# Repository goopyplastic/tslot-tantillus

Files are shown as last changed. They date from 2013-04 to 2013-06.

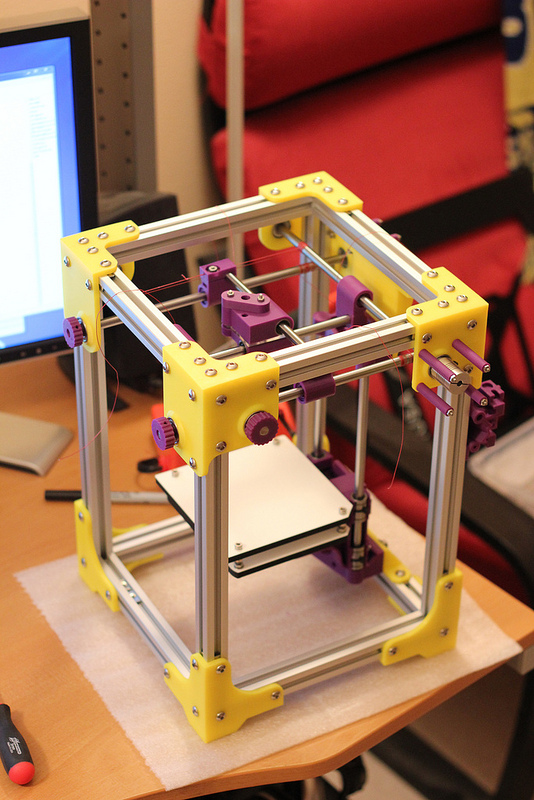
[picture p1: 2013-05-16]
photo.jpg

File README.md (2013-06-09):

tslot-tantillus
===============

T-Slot frame for Tantillus 3D Printer

Initial Version Assumes:

- That you are using the cable version of the Z axis. If you aren't you will need to modify the lower Z adaptor for motor mount holes.
- 40mm standoffs for motor mounts, can purchase at mcmaster or print your own. Use 3x50mm bolts to attach motors.
- Misumi 2020 T-Slot lengths:
     - 8x HFS5-2020-200 (Horizontal 200mm)
     - 4x HFS5-2020-335 (Vertical 335mm)
     - HNKK5-5 (T-Slot nuts)
     - M5 10mm button head screw to affix panels to frame
- 8mm Shafting
     - 2x SFJ8-170 (8x170mm bearing shafts, same as Tantillus internal XY axis)
     - 2x SFJ8-230 (8x230mm bearing shafts, same as Tantillus Z axis)
- 5/16" Shafting
     - 2x 277mm
     - 2x 277mm with holes drilled 56.5mm in from each end for a distance of 164mm hole to hole
- Couplers
     - 2x Aluminum or simlar 5mm to 8mm shaft couplers
- Frame extra STL's:
     - spacers.STL - Motor 40mm standoffs if you want to use printed ones
     - knob_fixed.stl - Collar/manual nob for end of 5/16" rod (Use m3 set screw to hold in place on shaft.)
     - fanmount_fixed.stl x2 - Clips to attach fans to t-slot
     - lcdclamp_fixed.stl x2 - Clips to use as a rest for http://www.thingiverse.com/thing:28767
     - megaholder_fixed.stl - Plate for attaching arduino mega to t-slot
- The following files are provided for convenience:
     - ZlowerbracketfixedMETRIC_fixed.stl - Cable Z bracket modd'ed for M5 mounting (Use M5 16mm and M5 nuts)
     - ZupperbracketfixedMETRIC_fixed.stl - Cable Z bracket modd'ed for M5 mounting (Use M5 16mm and M5 nuts)

BEEFY Z Option:

- Is a more rigid Z axis mounting that has some other advantages such as being able to slide the upper and lower mount around and clamping bar end holders.
- BEEFY Z Printed parts
     - Zlowerbracket_BEEFY.stl - Cable Z bracket modd'ed for M5 mounting (Mounts directly into 2060 T-Slot)
     - Zupperbracket_BEEFY.stl - Cable Z bracket modd'ed for M5 mounting (Mounts directly into 2060 T-Slot)
- Misumi 2060 T-Slot Lengths:
     - 1x HFS5-2060-295 (Vertical 295mm [40mm short of main uprights)
- Misumi 90 degree brackets:
     - 4x HBLFSN5
I'm often in #reprap as goopyplastic if you have questions!

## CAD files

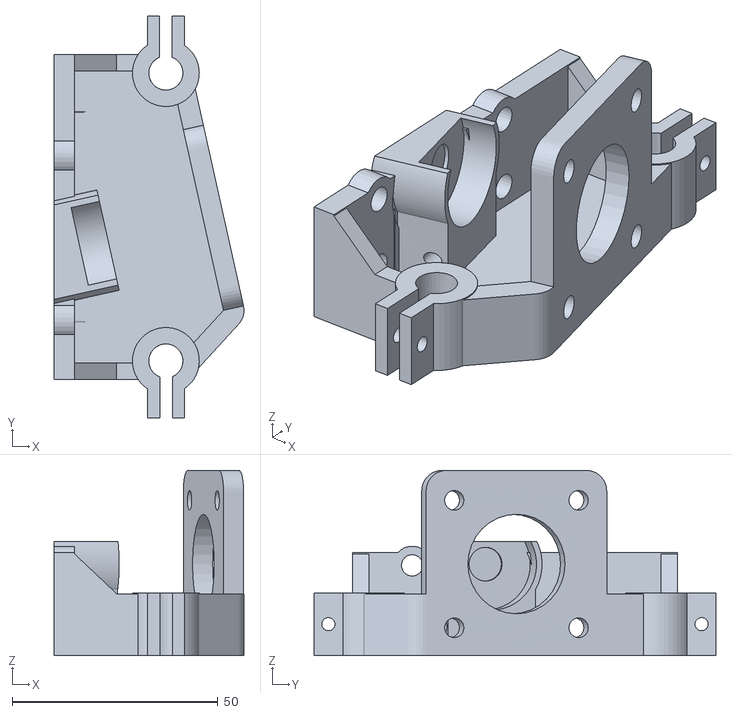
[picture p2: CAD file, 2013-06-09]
Zlowerbracket_BEEFY.stl
46.2 x 97.7 x 45.0

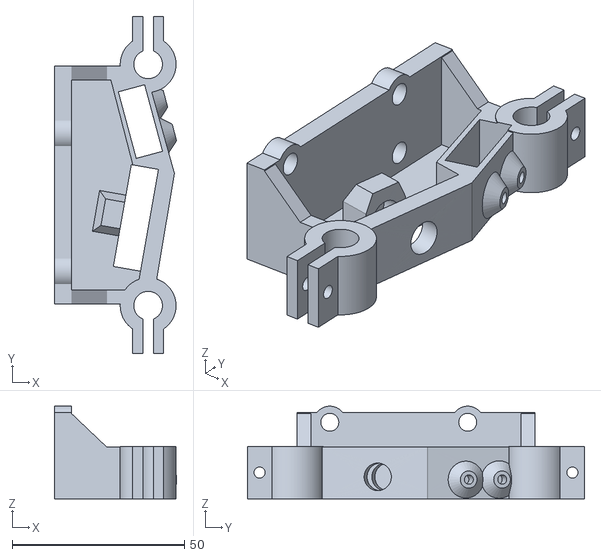
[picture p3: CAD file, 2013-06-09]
Zupperbracket_BEEFY.stl
35.5 x 97.8 x 26.9

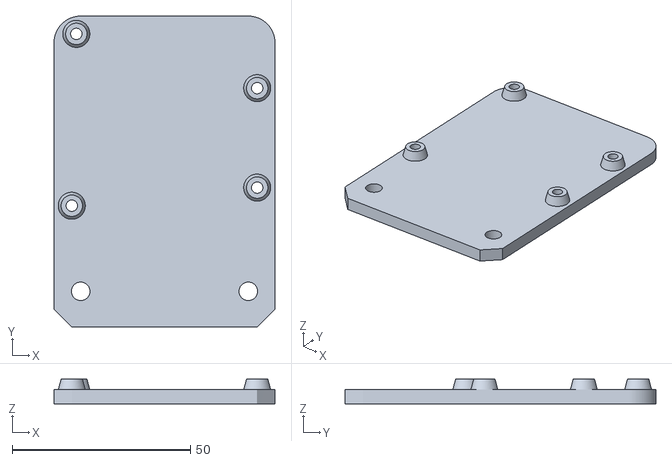
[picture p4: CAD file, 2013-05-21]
megaholder_fixed.stl
62.1 x 87.3 x 7.00

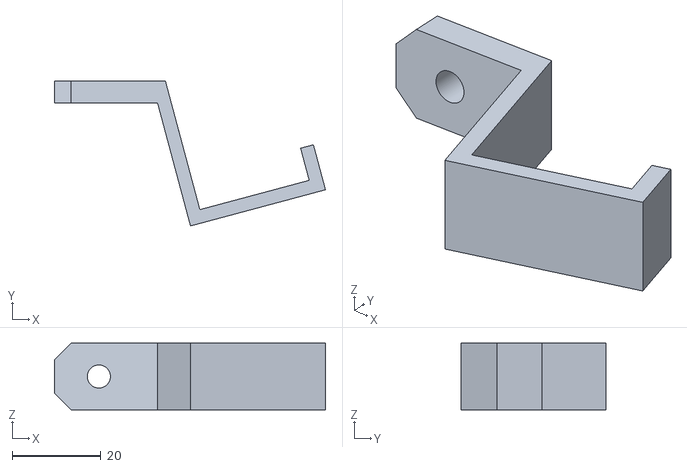
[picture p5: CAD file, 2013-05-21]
lcdclamp_fixed.stl
61.1 x 32.7 x 15.0

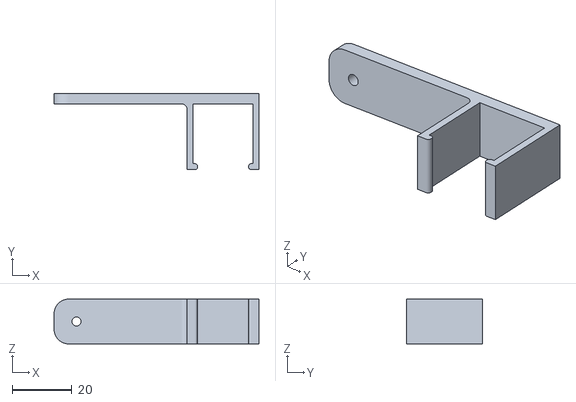
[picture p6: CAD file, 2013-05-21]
fanmount_fixed.stl
68.5 x 25.5 x 15.0

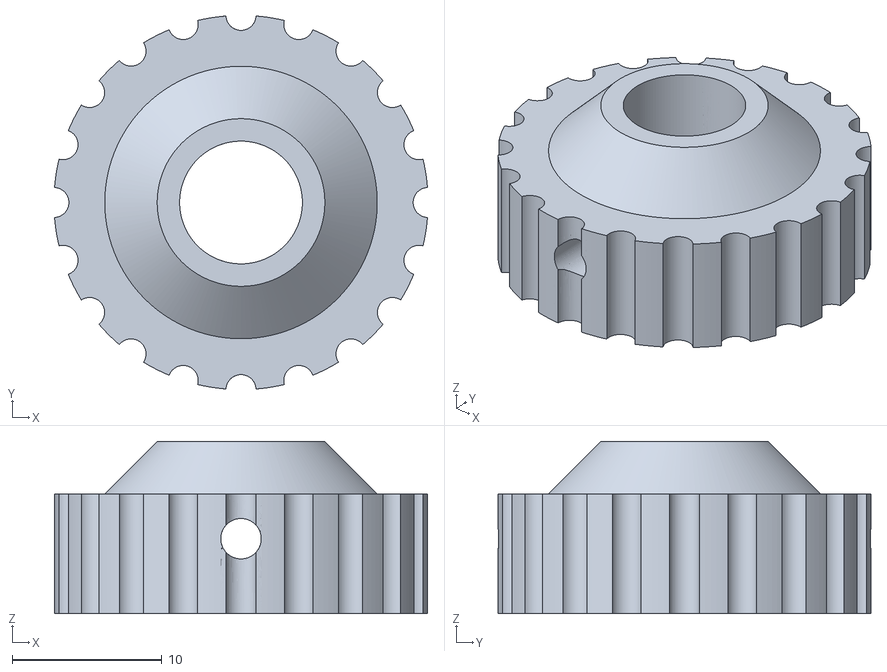
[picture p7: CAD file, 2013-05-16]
knob_fixed.stl
24.9 x 24.9 x 11.5

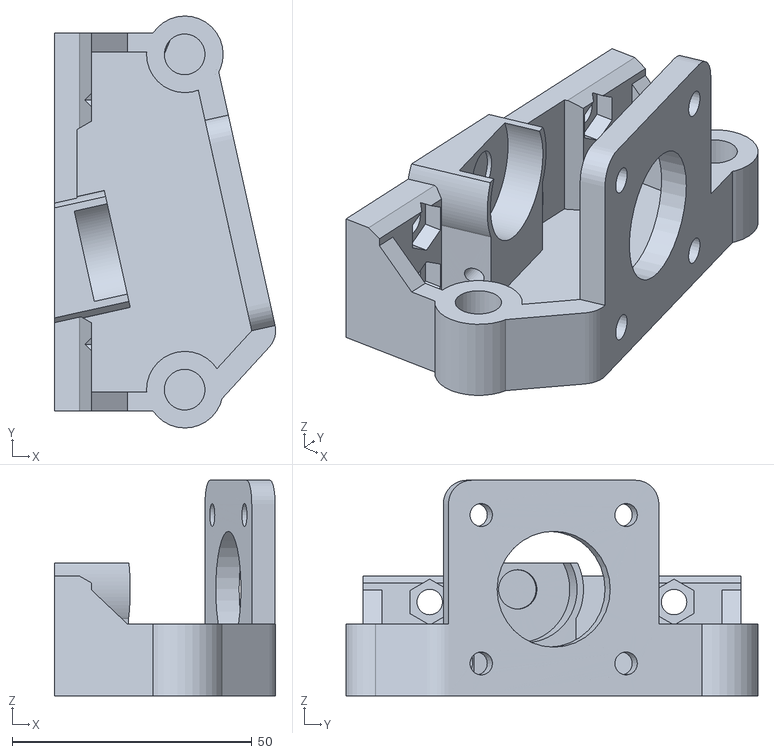
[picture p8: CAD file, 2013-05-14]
ZlowerbracketfixedMETRIC_fixed.stl
46.2 x 86.0 x 45.0

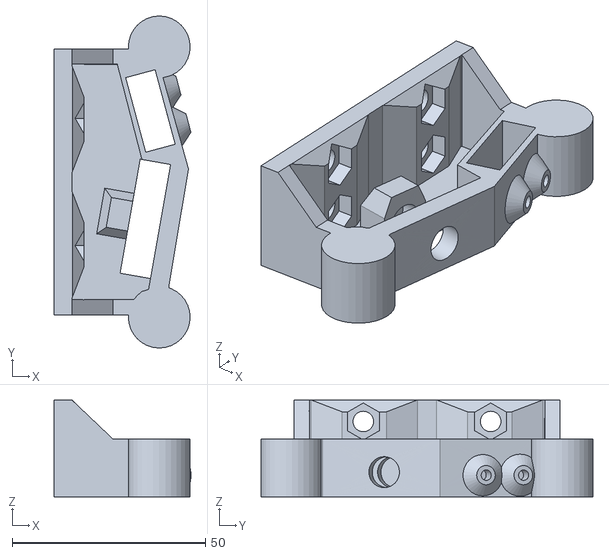
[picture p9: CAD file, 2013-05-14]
ZupperbracketfixedMETRIC_fixed.stl
35.5 x 86.0 x 25.0

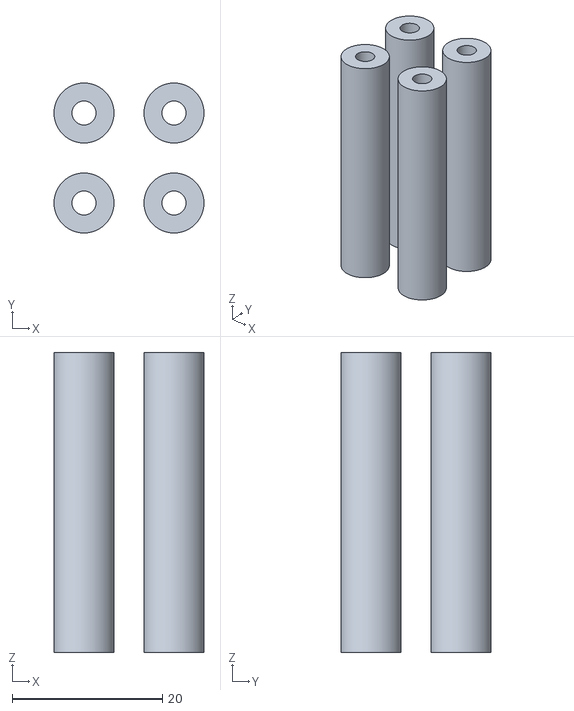
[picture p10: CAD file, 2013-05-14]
spacers.STL
20.0 x 20.0 x 40.0

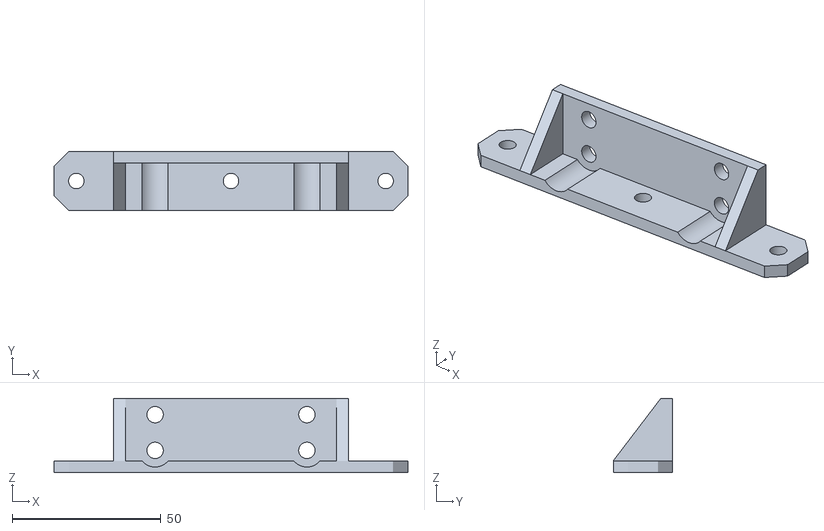
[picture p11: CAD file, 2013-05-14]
z_lower_adapter.STL
119.0 x 20.0 x 25.0

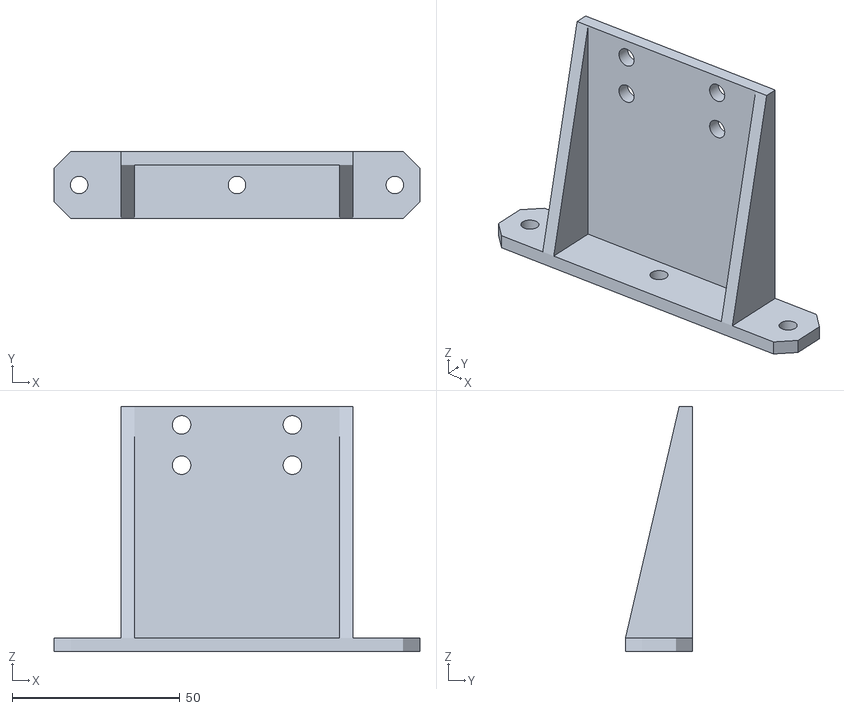
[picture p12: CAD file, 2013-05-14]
z_upper_adapter_long.STL
109.0 x 20.0 x 73.0

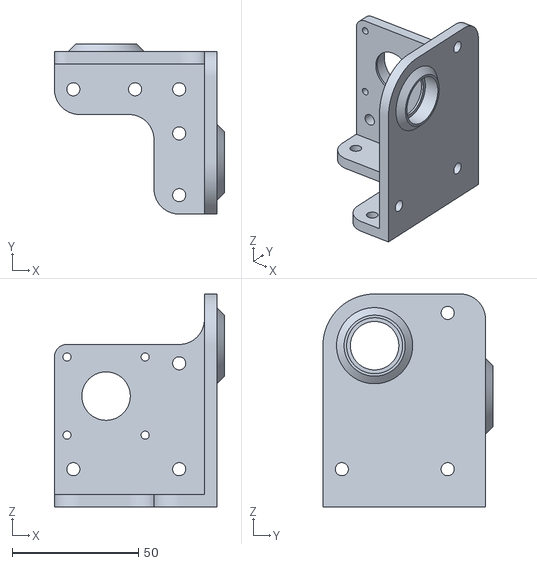
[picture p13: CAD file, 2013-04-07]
panel_combine_REAR_RIGHT.STL
67.5 x 67.5 x 84.5

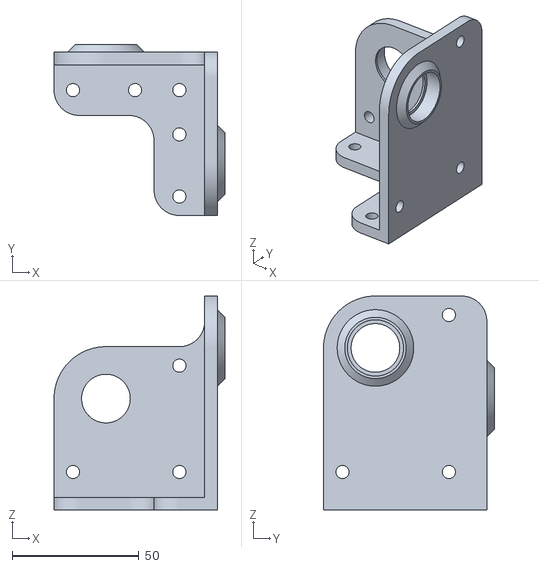
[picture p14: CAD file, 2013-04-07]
panel_combine_FRONT_LEFT.STL
67.5 x 67.5 x 84.5

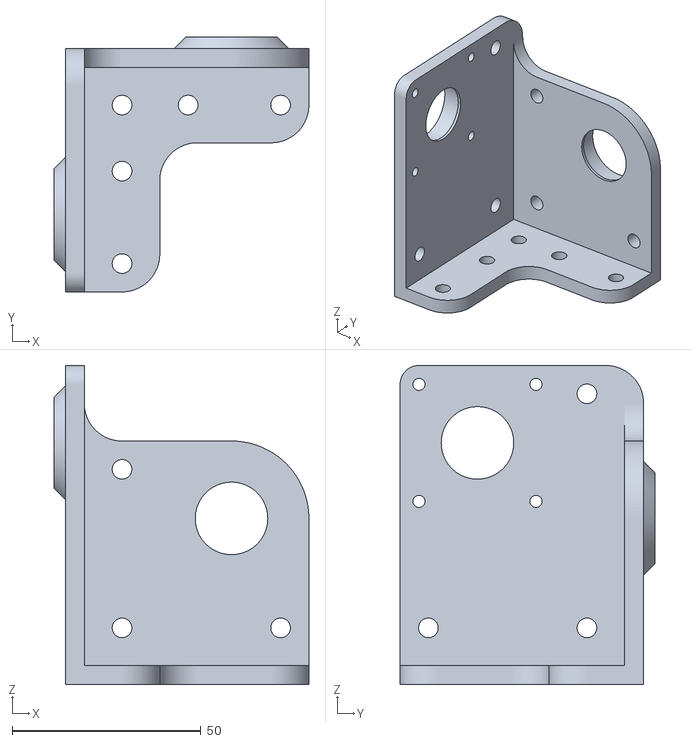
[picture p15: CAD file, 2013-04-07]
panel_combine_REAR_LEFT.STL
67.5 x 67.5 x 84.5

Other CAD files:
panel_combine_BOTTOM.STL
panel_combine_FRONT_RIGHT.STL

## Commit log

2013-04-07 initial upload
    [panel_combine_BOTTOM.STL, panel_combine_FRONT_LEFT.STL, panel_combine_FRONT_RIGHT.STL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]
2013-05-16 Integrated design increased binding issues
    [XYEndLeftINTEGRATED_fixed.stl, XYEndRightINTEGRATED_fixed.stl]
2013-05-16 Larger knob that fits better on shaft.
    [knob_fixed.stl]
